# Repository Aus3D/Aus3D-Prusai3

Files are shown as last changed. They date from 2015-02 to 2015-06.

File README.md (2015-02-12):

# Aus3D's Prusa i3 Repository
This is the page for all of the documentation and firmware relating to the Aus3D [Prusa i3 3D Printer kit](http://aus3d.com.au/3D-printers/printer-kits/i3-printer).

The firmware is a version of Marlin pre-customised and calibrated to suit our i3 kit. It can be found in the 'Marlin-Marlin_v1' folder.

Documentation can be found in the folder labelled 'Docs'.

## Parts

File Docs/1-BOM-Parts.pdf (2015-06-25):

# Aus3D Prusa Mendel i3 Kit

## (HC-101 Acrylic Frame 3D Printer)

## Bill of Materials

(Updated 4/12/2014)

### Congratulations on receiving your Aus3D Prusa Mendel i3 kit!

Each kit is checked before being sent out, but before you start building you should confirm you have

### all of the below components. If something is missing, let us know and we’ll fix it!

Electronics | | Extruder
Power Supply | 1 | Stepper Motor | 1
Melzi Controller | 1 | Hotend | 1
Stepper Motor (w/ leadscrew) | 2 | Thermistor | 1
Stepper Motor (w/GT2 pulley) | 2 | Ceramic Heater | 1
Heated Bed (w/ Thermistor and wires) | 1 | 40mm Fan | 1
Endstop | 3
AU Power Cable | 1 | Hardware
USB Cable | 1 | Acrylic Frame Pieces*
Silicone Wire | 1 | Bed Support Plate | 1
| | 8mm Smooth Rod | 6
Printed Parts | | M8 Threaded Rod | 4
X Motor Mount | 1 | M3 Screws (several sizes) | Packs
X Idler | 1 | M3 Nuts | Pack
Y Bearing Holder (attached to Bed Support Plate) | | M3 Spring Washers | Pack
Endstop Clip | 3 | M8 Nuts | 6
| | M8 Washers | 4
| | GT2 Belt | 2m
Misc. | | Spring | 4
Spiral Wire Wrap | 1 | Bearing (flanged) | 2
Cable Ties | Pack
Cable Tie Mounts | Pack
Kapton Tape | Roll | Tools
USB | 1 | Allen Key | 4
PLA Filament Sample | 1 | Side Cutters | 1

*See included acrylic pieces bill-of-materials

*** Aus3D does not replace missing parts reported more than 30 days after date of delivery ***

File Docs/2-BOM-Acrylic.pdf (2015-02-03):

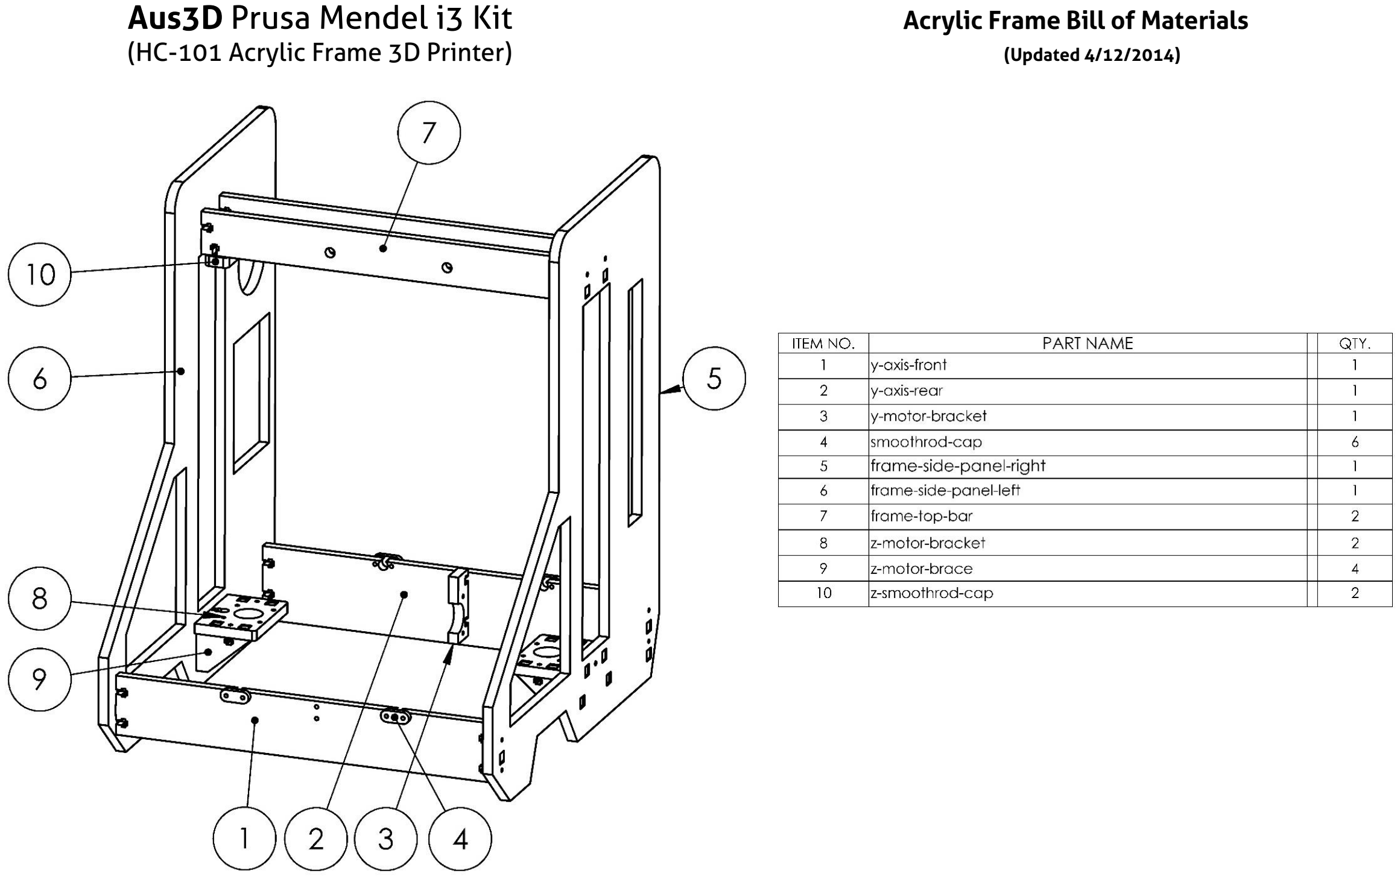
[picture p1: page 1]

Aus3D Prusa Mendel i3 Kit | Acrylic Frame Bill of Materials
(HC
-101 Acrylic Frame 3D Printer
) | (Updated 4/12/2014)

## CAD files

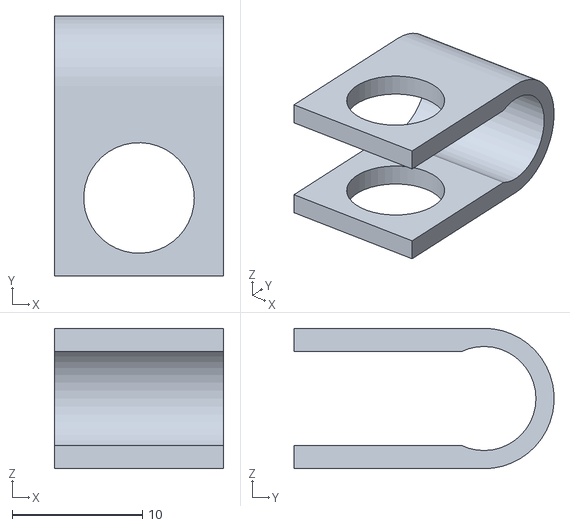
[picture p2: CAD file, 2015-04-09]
FrameSTLs/filament-clip.STL
13.0 x 20.0 x 10.8

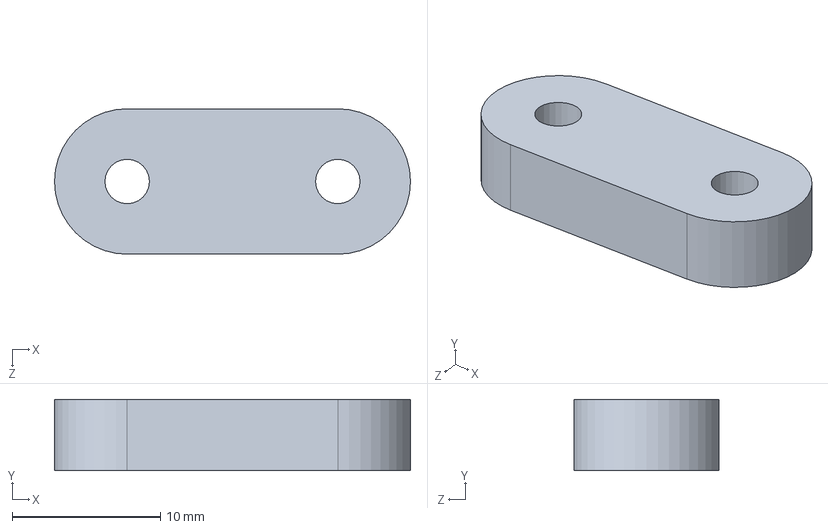
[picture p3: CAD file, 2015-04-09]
FrameSTLs/Source/smoothrod-cap.SLDPRT
24.0 x 4.80 x 9.80 mm

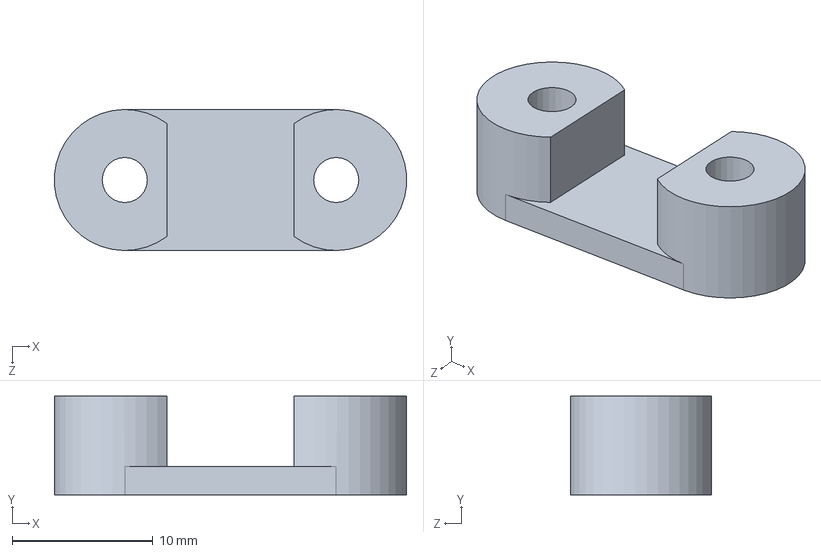
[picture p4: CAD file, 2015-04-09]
FrameSTLs/Source/y-belt-holder.SLDPRT
25.0 x 7.00 x 10.0 mm

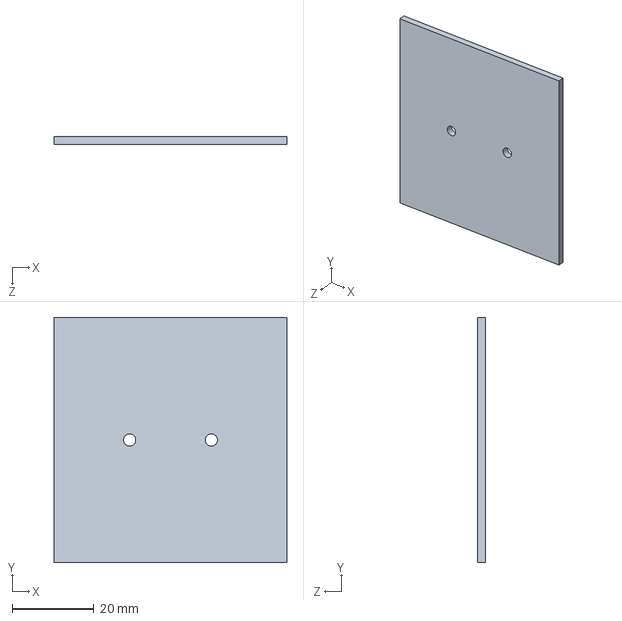
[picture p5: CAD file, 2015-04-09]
FrameSTLs/Source/extruderPlate.SLDPRT
57.0 x 60.0 x 2.00 mm

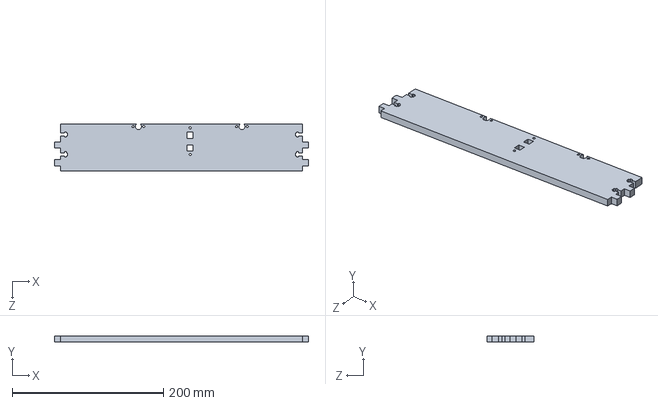
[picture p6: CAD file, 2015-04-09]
FrameSTLs/Source/y-axis-rear.SLDPRT
336.0 x 8.40 x 62.0 mm

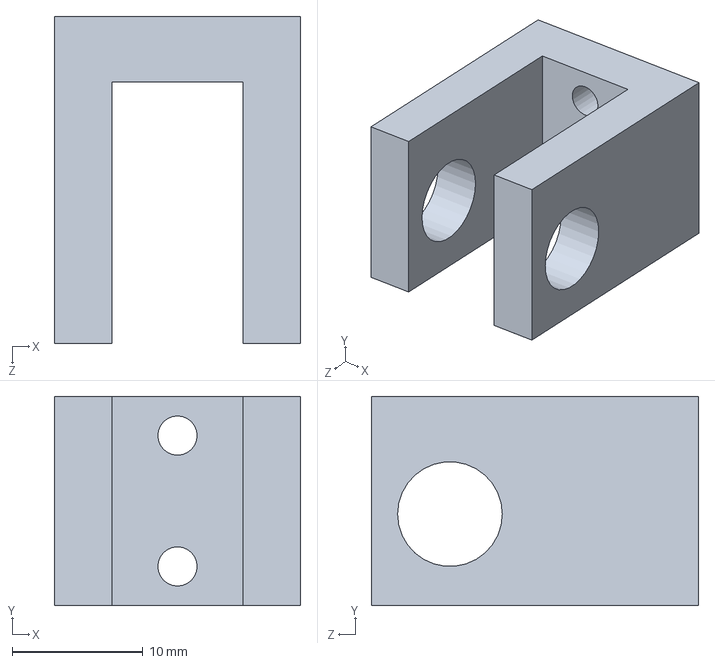
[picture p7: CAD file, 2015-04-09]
FrameSTLs/Source/y-idler.SLDPRT
18.8 x 16.0 x 25.0 mm

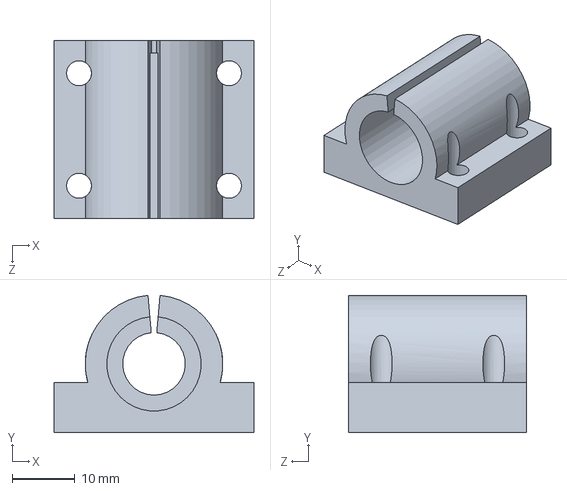
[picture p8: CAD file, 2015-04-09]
FrameSTLs/Source/y-bed-bearing-holder.SLDPRT
32.0 x 22.0 x 28.5 mm

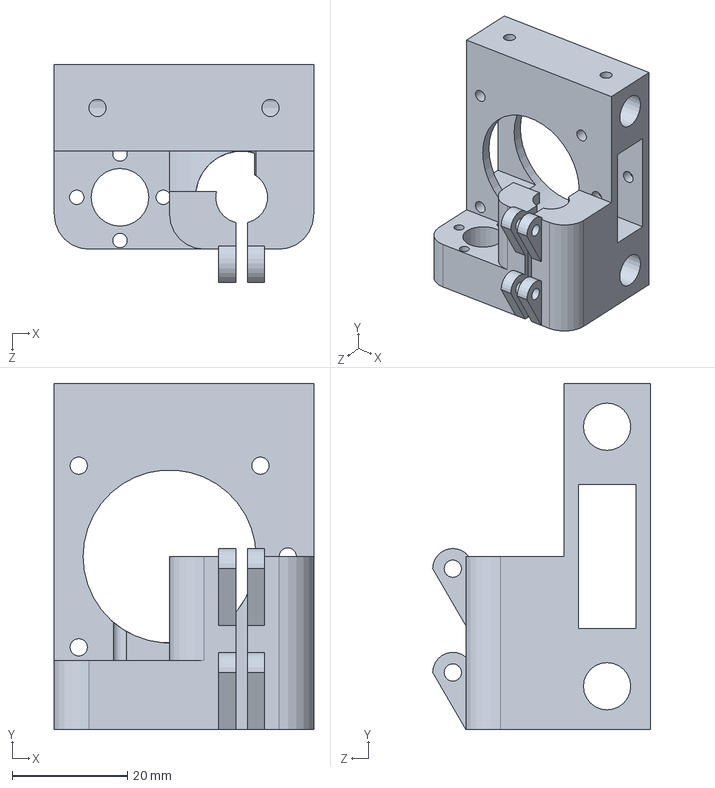
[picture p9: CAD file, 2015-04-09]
FrameSTLs/Source/x-motor-mount-new.SLDPRT
45.0 x 60.0 x 37.8 mm

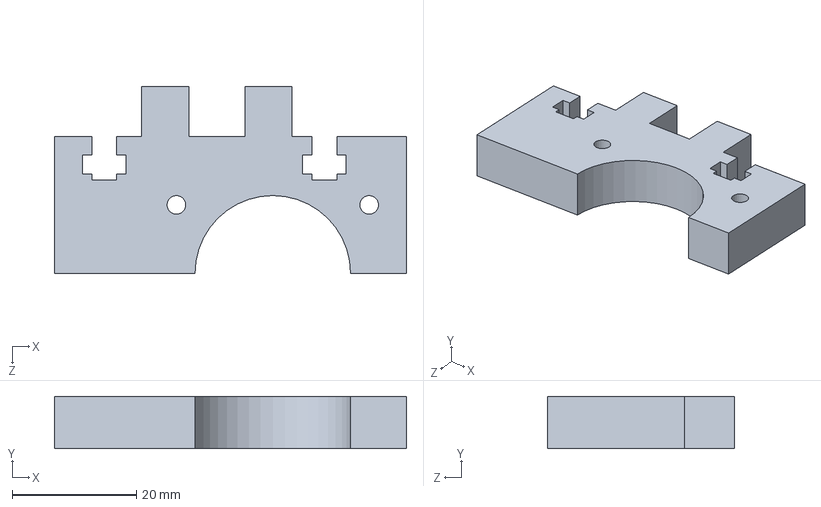
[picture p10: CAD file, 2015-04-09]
FrameSTLs/Source/y-motor-bracket.SLDPRT
56.6 x 8.40 x 30.0 mm

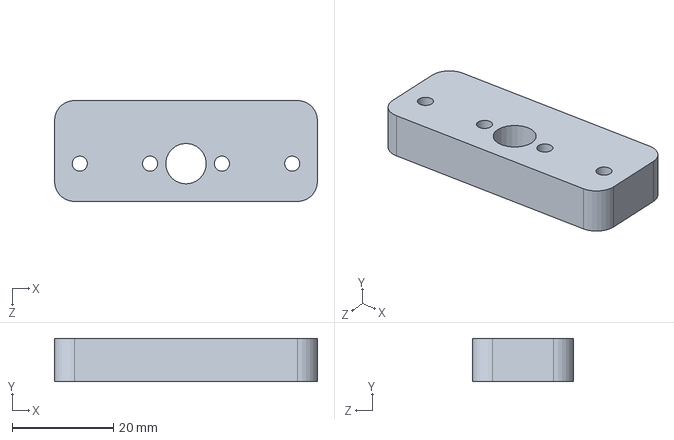
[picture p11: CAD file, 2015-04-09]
FrameSTLs/Source/z-smoothrod-cap.SLDPRT
52.0 x 8.60 x 20.0 mm

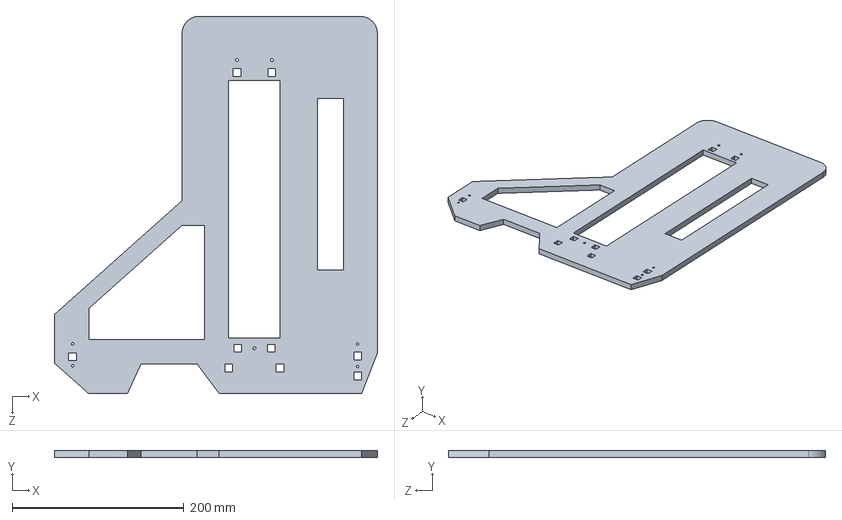
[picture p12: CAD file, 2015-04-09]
FrameSTLs/Source/frame-side-panel.SLDPRT
376.5 x 8.40 x 439.9 mm

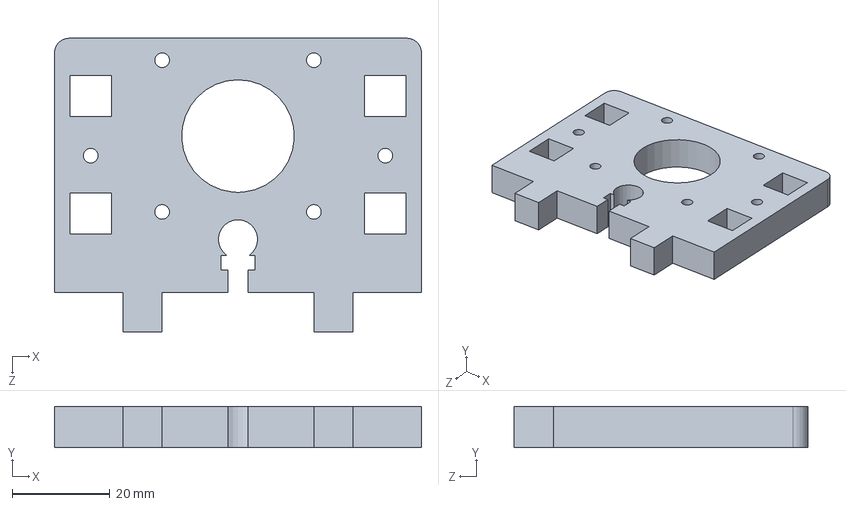
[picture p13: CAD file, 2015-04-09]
FrameSTLs/Source/z-motor-bracket.SLDPRT
75.0 x 8.40 x 60.0 mm

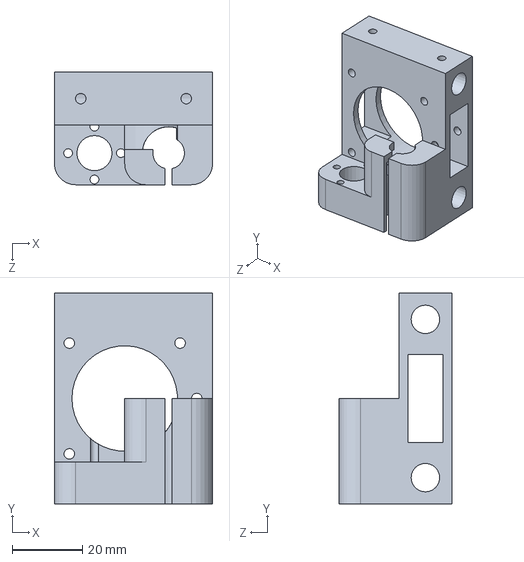
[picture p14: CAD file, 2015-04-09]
FrameSTLs/Source/x-motor-mount.SLDPRT
45.0 x 60.0 x 32.0 mm

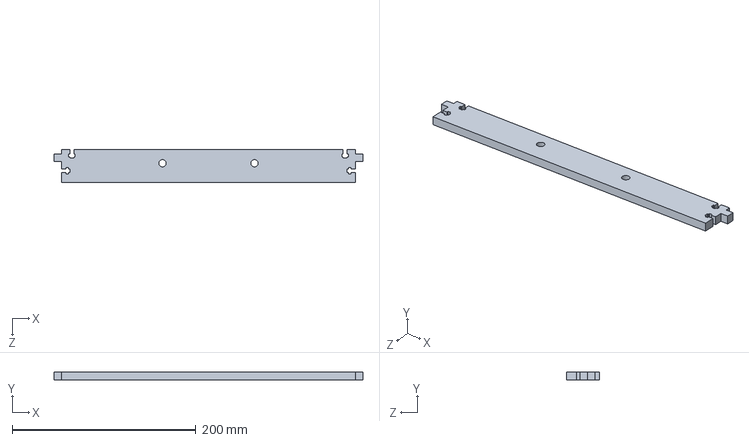
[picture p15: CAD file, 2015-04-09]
FrameSTLs/Source/frame-top-bar.SLDPRT
336.0 x 8.40 x 36.0 mm

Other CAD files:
FrameSTLs/Source/x-idler-mount.SLDPRT
FrameSTLs/Source/frame-side-panel-right.SLDPRT
FrameSTLs/Source/z-motor-brace.SLDPRT
FrameSTLs/Source/y-axis-front.SLDPRT
FrameSTLs/Source/frame-side-panel-left.SLDPRT
FrameSTLs/Source/x-idler-mount-new.SLDPRT
FrameSTLs/Source/y-support-plate.SLDPRT
FrameSTLs/frame-side-panel-left.STL
FrameSTLs/frame-side-panel-right.STL
FrameSTLs/frame-top-bar.STL
FrameSTLs/smoothrod-cap.STL
FrameSTLs/x-idler-mount.STL
FrameSTLs/x-motor-mount.STL
FrameSTLs/y-axis-front.STL
FrameSTLs/y-axis-rear.STL
FrameSTLs/y-bed-bearing-holder.STL
FrameSTLs/y-belt-holder.STL
FrameSTLs/y-idler.STL
FrameSTLs/y-motor-bracket.STL
FrameSTLs/y-support-plate.STL
FrameSTLs/z-motor-brace.STL
FrameSTLs/z-motor-bracket.STL
FrameSTLs/z-smoothrod-cap.STL

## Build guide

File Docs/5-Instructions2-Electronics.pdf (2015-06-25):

© 2015 Aus3D, All Rights Reserved. | V1.1

## Aus3D Prusa Mendel i3 Kit

Electronics Assembly Instructions

Section 1 - Electrical

1. Complete frame construction – see “instructionsV1.pdf”.
2. Install the power supply unit (PSU). The PSU mounts to the left side of the frame, and

# uses 4 M3 screws. Make sure to use the plastic spacers included - the screws shouldn't go too far (more than 3-4mm) inside the PSU. The electrical connections should face

downwards to make for neater cabling.
3. Install the Melzi control board. The control board mounts to the right side of the frame.

Plastic spacers are included in each kit, place spacers between the board and the frame before screwing it in place. Mount the control board so that the USB and microSD connections are near the top.
4. Install the cable that carries power from the PSU to the control board. This is a 2-core

cable (usually red and black). On the control board, the cable wires into the terminal marked “POWER”. The upper connection (near “HOTBED”) is negative, the lower connection (near “E-MOTOR”) is positive.

On the PSU the red wire should go to any of the DC Output terminals marked positive, and the black to any marked negative. All the positive terminals are identical, and all the negative terminals are identical – there is no preference where the wires connect, but keeping them further apart may reduce the risk of an accidental short.
5. Wire the motors to the control board. There are two different sets of coloured wires that

the motors may have. Depending which colours are present, wire the motor cables in the following order (top-to-bottom):

Black, Green, Blue, Red
or
Yellow, Blue, Green, Red

Motors wired incorrectly may move in reverse, or not move at all. However, there is no risk of damaging the motors due to incorrect wiring order.

If a motor runs in reverse, switch the first (or last, but not both) two wires around (e.g. swap black and green, or yellow and blue).

Because there are two motors for the Z axis, they will both need to be wired into the same terminals. Twisting the ends of the wires (e.g. both sets of red, etc.) together may make this easier.

6. Install the heated bed. Use 4 longer M3 screws (20-24mm), a washer on top of the bed, a spring (not washer, full spring) in between the bed and the bed support plate, and a washer and nut beneath the bed support plate.

These screws can be adjusted to raise or lower each corner of the bed in order to get it level. The springs provide some protection should the hot-end crash into the print bed.

The power cable going to the heated bed (thicker wires) connects to the “HOTBED” terminal on the control board. Polarity matters, follow the convention established for the “POWER” terminal – the wire nearest “POWER” should be positive.

The two white wires from the heated bed are wired to the thermistor, and connect to the “BTEMP” terminal. Polarity does not matter.

To level the heated bed, move the extruder down until the nozzle is a paper’s width from the bed surface. Now, move the extruder from left to right and verify that the distance remains constant. Adjust if necessary. Move the printer bed back and forth, again, monitor the distance and adjust if necessary.

7. Wire the extruder (motor should already be done. If not, do it first). The white wires (thermistor) connect to “ETEMP”, polarity does not matter. The red wires (heating element) connect to “HOTEND”. Again, polarity does not matter. The fan wires connect to “FAN”, and polarity matters. The positive wire is near “HOTEND”.
8. Now it is time to install and wire up the endstops (microswitches). Included are three plastic clips that the endstops will screw onto. The clips will hold the endstops onto 8mm smooth rod, and should be tightened in place securely. Below is a diagram of endstop placement:

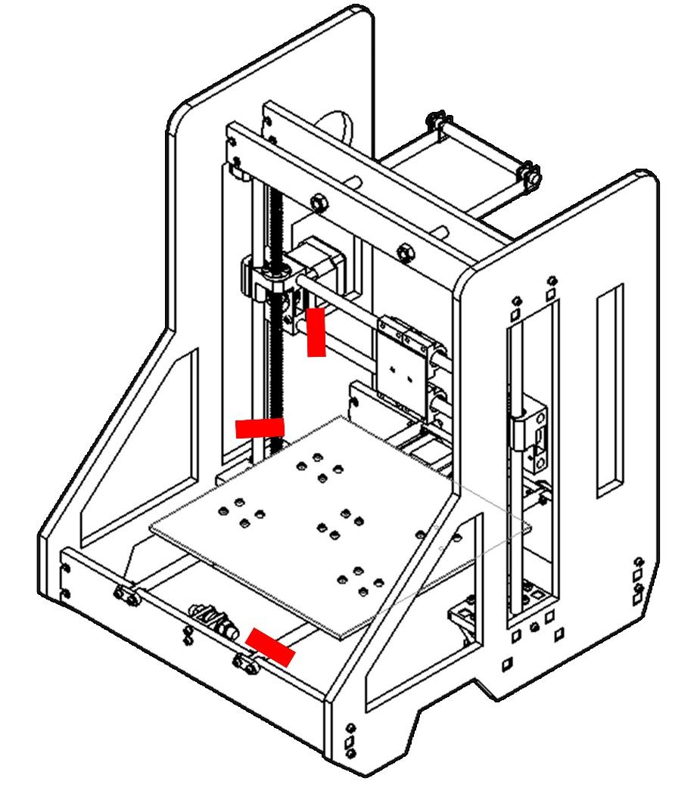
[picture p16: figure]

Verify that each switch will make contact with the moving components. The X endstop should be pressed by the extruder carriage, the Y endstop should be pressed by the printer bed, and the Z endstop should be pressed by the X motor mount.

Wire the endstops to the control board. Polarity does not matter. Endstops are marked “XSTOP”, “YSTOP” and “ZSTOP”.

9. Wire the included mains-lead to the PSU. For safety, ensure the cable is NOT connected to mains power while doing this step.

AU mains colour coding is as follows:

NEUTRAL – Black or Blue
LINE/ACTIVE – Red or Brown
EARTH – Green or Yellow

The PSU should have three terminals for the mains connection (AC Input), marked L, N and GND (or GND symbol, ).

Once the wires are securely in place, the cable may be plugged into mains power.

Section 2 – Software / Firmware

# 1. Download the Arduino IDE (version 1.0.5 recommended) from:

http://arduino.cc/en/Main/Software

2. Download the “Sanguino” folder from https://github.com/reprappro/Marlin. To do this, use the “Download Zip” button on the right of the page, and extract the “sanguino” folder somewhere you can find it.

Place the “sanguino” folder into Arduino hardware folder. On Windows, this is found at: C:\Users\USERNAME\Documents\Arduino\hardware

This should make the new structure C:\Users\USERNAME\Documents\Arduino\hardware\sanguino

3. Turn the power to the printer (mains power) on, and connect the USB cable between the printer and your computer. Your computer should automatically download and install the appropriate drivers. If not, drivers can be found on this USB.
4. Download the Aus3D customised firmware from https://github.com/Aus3D/Prusai3. Use the “Download ZIP” button as before. Extract the files, and open “Marlin.ino” with the Arduino software.
5. In the Arduino software, select the open file “Configuration.h” from the top bar of open files. The following lines will need to be adjusted later to properly calibrate distances:

// default settings
#define DEFAULT_AXIS_STEPS_PER_UNIT {78.7402,78.7402,200.0*8/3,760*1.1}

#define DEFAULT_MAX_FEEDRATE | {500, 500, 5, 25} // (mm/sec)

#define DEFAULT_MAX_ACCELERATION | {9000,9000,100,10000}

6. In the Arduino software, select “Tools”>”Board”>”Melzi 1284p 16mhz”.
Select “Tools”>”Serial Port”, and select the highest-numbered COM port.
7. Press the “Upload” (play) button to upload the firmware to the board. It may take a minute, but there should be a message informing you of a successful upload in the bottom terminal window. If there is not:
a. Double check the COM port. Verify this is the correct COM port by opening device manager and looking for Melzi. Alternatively, unplug the board to see which COM port disappears.
b. If problems persist, unplug the USB cable, wait a few seconds, and plug it back in. Select the correct COM port and try again.
c. Sometimes pressing the “Reset” button on the Melzi board before / during the start of the upload can help resolve issues.
8. Download the latest version of Printrun (or use the copy provided on the USB) and extract the software. Open “Pronterface”.

9. In Pronterface, set the Port to the known COM port, and the number (BAUD rate) to 115200 (which was pre-set in the firmware we uploaded). Press connect, and after a moment the console window in Pronterface should report success.
10. Position the extruder (by hand) in the middle of the X axis, so that if it moves the wrong way nothing will be damaged. Then, in Pronterface, use either the + or – X button to move the axis. Move the axis in short motions at first, until you are sure it is moving correctly. Do not move the axis far enough to crash into the frame.
11. Perform the same check for the Y and Z axis. They should each move as told. If any of the axis seem to move in the wrong direction, you can either switch the motor wires (as discussed previously) or change the firmware line (select appropriate axis, change false->true or vice-versa):

#define INVERT_X_DIR false

12. Now, test that the X axis homes correctly. Be ready to unplug mains power quickly, if something goes wrong here the printer will make an unpleasant sound – but it shouldn’t be damaged.

Move the extruder to the middle of the axis (electronically), and then press the X home button (X with a house). The carriage should move towards the switch, and once it presses the switch, it should stop moving.

If the axis moves the wrong way (away from the switch), verify:
-Where the switch was placed, relative to the diagram previously.
-That the motor moves in the correct direction under manual control.

If the axis does not stop, verify:
-That the carriage physically presses the switch on contact.
-That the switch is wired to the control board correctly.
13. Repeat these checks for the Y and Z axes. Again, be prepared to unplug the printer if something goes wrong.
14. Once each endstop has been tested and confirmed working, you may home all three axes. Press the home button without a letter – first the X axis will home, then Y, and then Z. This will happen automatically at the start of every print, so verify that no cables are going to get caught or stuck during this motion.
15. When an axis is homed, software defined limits are placed at the opposite end of the axis. The firmware included comes with limits of 150mm for the X any Y axis, and 180mm for the Z axis. Be ready with the power switch just in case! Verify that these limits are working by telling the software to move an axis repeatedly away from the endstop. Before the axis reaches the end, it should stop automatically, and not move any further.

These limits are pre-set as safe limits for getting setup and testing. To change these limits, edit the following lines in the firmware:

// Travel limits after homing #define X_MAX_POS 150
#define X_MIN_POS 0

#define Y_MAX_POS 150

#define Y_MIN_POS 0

#define Z_MAX_POS 180

#define Z_MIN_POS 0

16. Verify that the thermistors are operating correctly. The “Check Temp” button should return the temperature for the extruder and the bed.
17. Verify that the extruder and bed can both heat up correctly. Set the temperature to a full integer (60 for bed, 180 for extruder are common numbers for PLA) and press “Set”. You should see the temperature reach these numbers over a few minutes.

Do not touch the hotend while it is heating up! The heated bed gets toasty too!

18. Once at temperature, carefully feed some PLA filament through the extruder and into the hotend. Once the filament is correctly placed, and there is a gap between the nozzle and the bed (raise the Z axis), press “Extrude”. The extruder motor should activate and push the filament into the hot-end.

You may need to press the button several times (or adjust the extrude length) before any filament comes out the nozzle. If the motor spins the wrong way, see previous info regarding reversing the motors.

Note: Pronterface will for some reason return an error message if the extruded length or rate are decimal values – ensure they are integer numbers with no decimal point.

19. Congratulations – at this stage, everything should be working and you should be ready to do a test print – and start calibrating! Calibration is far too broad a topic to be encompassed in this guide – an excellent starting point is the following wiki page:

http://reprap.org/wiki/Calibration

Finally, if you are stuck and need assistance, please contact me via chris@aus3d.com.au.

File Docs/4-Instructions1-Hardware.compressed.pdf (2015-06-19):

Components:
2M3x16Screws
2M3SpringWashers
2M3HexNuts
AssembledZbrackets
AcrylicSidePanels

Attachtheassembledmotorbrackets totheacrylicsidepiecesoftheframe.

Seethebelow imagesfororientation.

Components:
2M3x16Screws
2M3SpringWashers
2M3HexNuts
1Z-motor-bracket
2Z-motor-braces

RepeatforthesecondZmotorbracket. Theacryliccomponentshaveno orientationandareinterchangeable.

Components:
2M3x16Screws
2M3SpringWashers
2M3HexNuts
1Z-motor-bracket
2Z-motor-braces

AssemblethefirstZmotorbracket usingtheabovecomponents.Takecare nottoovertightenthescrews.

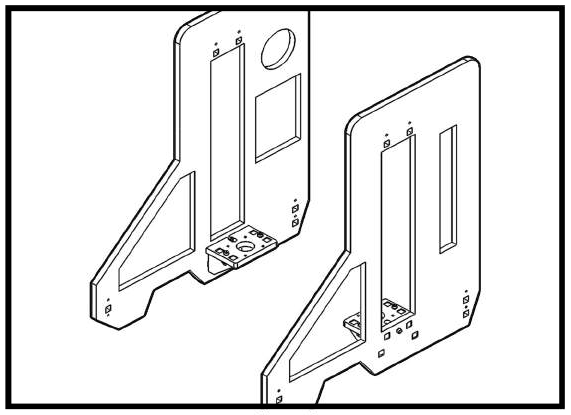
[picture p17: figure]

© 2015Aus3D,AllRightsReserved. | Page1

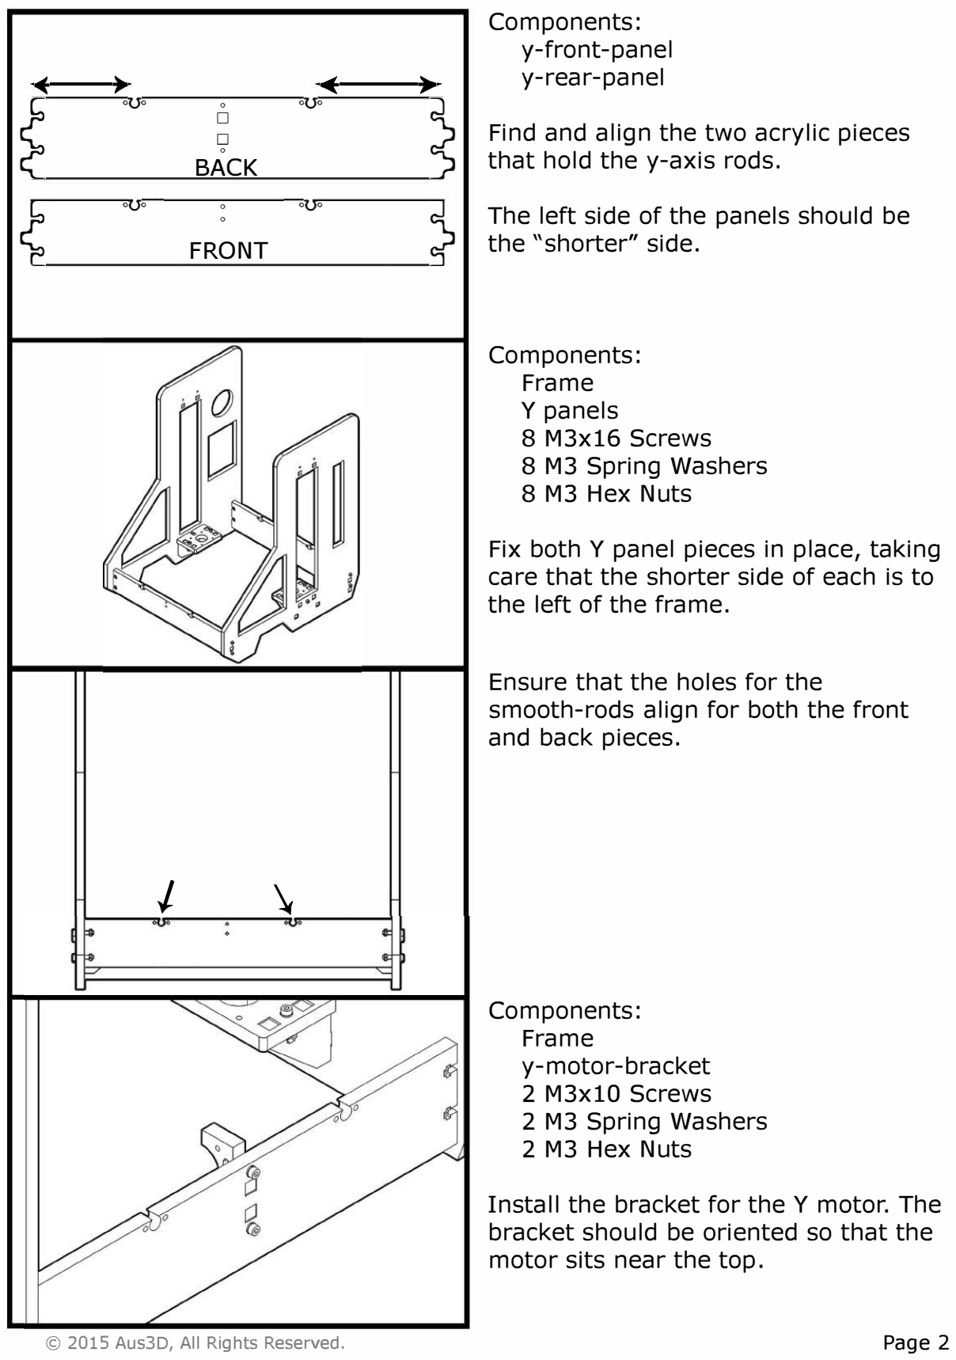
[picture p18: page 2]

-E |

ouo

ouo

0
D
D

0
BACK

0

0
FRONT

J \

ouo

ouo

© 2015 Aus3D, All Rights Reserved.

y-front-panel
y-rear-panel

Find and align the two acrylic pieces that hold the y-axis rods.

The left side of the panels should be the "shorter" side.

Components:
Frame
Y panels
8 M3x16 Screws
8 M 3 Spring Washers
8 M3 Hex Nuts

Fix both Y panel pieces in place, taking care that the shorter side of each is to the left of the frame.

Ensure that the holes for the smooth-rods align for both the front and back pieces.

Components:
Frame
y-motor-bracket
2 M3x10 Screws
2 M 3 Spring Washers
2 M3 Hex Nuts

Install the bracket for the Y motor. The bracket should be oriented so that the motor sits near the top.

Components:
BedSupportPlate
YBearingHolders(attachedtoabove)
28mm SmoothRods(~ 345mm)

Slidethesmoothrodsthroughthe frontY-plate,thenthroughtheY bearingholders(andbearings)and finallythroughtherearY-plate.

Checkthatthebedcanmovealongthe rods.

Components:
Frame
StepperMotor(longshaft)
2M3x12Screws
2M3SpringWashers

Checkthetwosteppermotorswith attachedpulleys.Insomekits,one motorhasalongershaft.Ifthisisthe case,usethismotor.

FixthismotortotheYmotormount.

Components:
Frame
y-idler
2M3x16Screws
2M3SpringWashers
2M3HexNuts

Attachthey-idlertothefronty-plate oftheframe.Thescrewsandnuts shouldnotinterferewiththebearings.

y-idler(plasticpart)
M8Rod(small)
2FlangedBearings
2M8Washers
2M8HexNuts

Fittheflangedbearingsintothey-idler asshown.

Theplasticpartmayneedtobe
cleaned/drilledout.

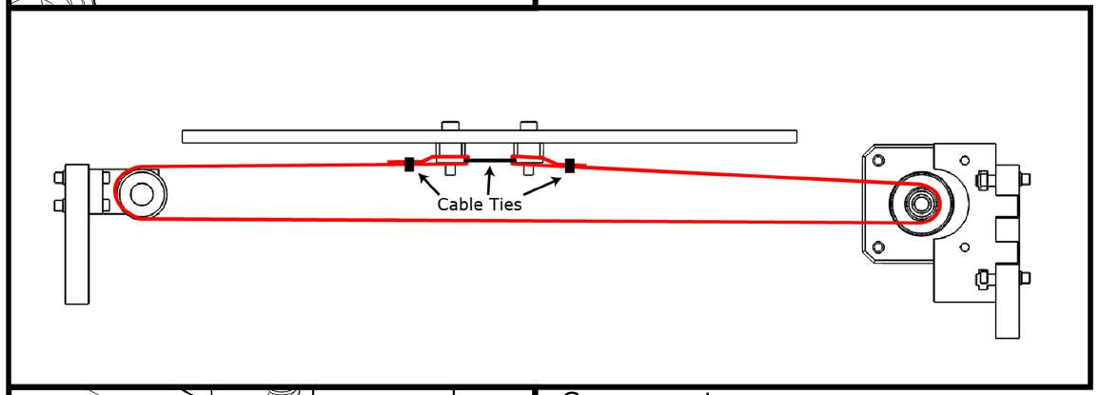
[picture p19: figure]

Components:
Frame
2Zmotors(withleadscrew)
8M3x14Screws
8M3SpringWashers

FixeachZmotortooneoftheZmotor brackets.

Removethecarriage-nutfrom each leadscrew.

Components:
Frame
GT2Belt(~ 0.8m)

Arrangethebeltasshowninthe diagram below.

Useacabletiebetweenthetwoends ofthebelttopullittaut.

Verifythatthebedcanmovefreely.

Frame
4Smoothrod-caps
8M3x16Screws
8M3SpringWashers
8M3HexNuts

Installthesmallacryliccappiecesat eachendofbothsmooth-rods.

Components:
XCarriage
XMotor(shortshaft)
3M3x14Screws
3M3SpringWashers

AttachtheXmotortothemountas shown.

Components:
XCarriage

SlidetheXCarriage(attachedtothe extruder)ontotheXaxissmoothrods.

PressthesmoothrodsintotheXIdler. Ifneccessary,carefullyhammerthe Idlerintoplace.

Components:
XMotorMount
XIdlerMount
28mm SmoothRods(~300mm)

PressbothsmoothrodsintotheX MotorMount.Theplasticmayneedto bedrilledslightlytoallow therodtofit.

Thefitshouldbefirm enoughto preventtherodsfrom movingfreely.

2CarriageNuts
XMotorMount
XIdler
8M3Screws

Installacarraigenutonboththe plasticpartsasshown.

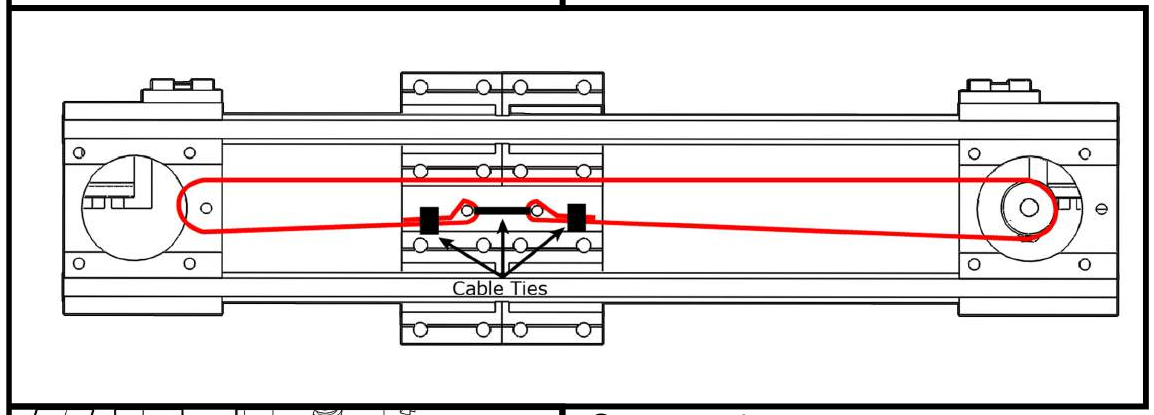
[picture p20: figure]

SlidetheX-axisontotheZ-axissmooth rods.Turntheleadscrew rodsbyhand tolowertheX-axis.

ManuallymovetheX-axisdown.Check thatitcanreachdowntothebed withoutissue.

Checkthedistancebetweenthe X-motormountandX-idlerifproblems occur.

Components:
Frame
28mm SmoothRods(~320mm)

InserttheZ-axissmoothrodsintothe cutoutsintheZmotorbrackets.The smoothrodsshouldsitonthe
Z-motors.Thescrew holdingthe Z-motorbracketsinplacemayneedto beloosenedslightly.

GT2Belt(~0.8m)
CableTies

InstalltheGT2beltontheXaxisas showninthebelow diagram.
(Diagram isreverseview,motoron right)

Usethecentercabletietotensionthe belt.

Pushtheplasticclipsontotheendof eachthreadedrod.

Slidethethirdthreadedrodthrough thefirstplasticclip.

Ifyouhaveaspooloffilamentready, placeitbetweentheclipsnow.

Pushtherodthroughthespooland intotheotherplasticclip.

Components:
Frame
3M8ThreadedRods
4M8Nuts
2PlasicSpoolClips

Slidethetwolongerthreadedrods throughthecutoutsinthetoppiecesof theframe,thenfixthem inplacewith theM8nuts.

Components:
Frame
2Z-smoothrod-caps
2Smoothrod-caps
4M3x16Screws
4M3SpringWashers
4M3HexNuts

FitthecapsthatholdtheZ-smoothrodsinplace.

Frame
2Frame-top-bars
4M3x16Screws
4M3SpringWashers
4M3HexNuts

Installthetwoacrylictop-barpieces ontotheframe.

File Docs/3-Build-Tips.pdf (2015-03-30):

Last updated: 30/3/2015 | V1.2

## Aus3D Prusa Mendel i3 Kit

(HC-101 Acrylic Frame 3D Printer)

Note: Copies of this documentation, along with other relevant files, can be found at: http://github.com/Aus3D/Prusai3 Tips:
- Use an included spring-washer on every bolt (where possible). This reduces the likelihood of damaging the acrylic.
- Take care not to over tighten any of the screws or bolts, as acrylic is not flexible and will snap suddenly if it experiences too much force. Generally, all screws and bolts should tighten until they feel fairly secure, do not tighten them further.
- Take care in aligning the acrylic supports for the y-axis – while they will fit in both ways, both the front and back must line up.
- Remember to put the y-axis printer bed support (large sheet with printed bearing holders) onto the 8mm smooth rods before fixing the smooth rods in place.
- Assemble the x-axis before placing it onto the z-rods.
- When wiring, take care to position all cables so that they will not get caught in moving parts. Cable ties, cable tie sticky mounts and cable loom is provided to help keep things tidy. Move each axis by hand to ensure cables will not get caught.
- Calibration is generally the hardest part of any printer build. Repetition is unfortunately the key, but a few things to check are:
- X/Y/Z axis are all as square as possible.
- Endstops are correctly positioned
- Hot-end nozzle is 1 layer height (0.2-0.4mm, use a sheet of paper to check) above printing surface.
- Bed is level (check each corner and centre)
- Some printed parts may vary slightly from kit to kit. Do not be alarmed if the parts you receive are not identical to those pictured in the assembly guide, as parts are revised and updated regularly.
- Screw sizes listed in the assembly manual are a guide only. The thickness of some parts varies from kit to kit, and different sized screws may need to be used. The included screws should be sufficient. Make sure screws used are long enough to thread into the nut, but not long enough to press into the acrylic frame (for T-slot joins).
- Finally, superglue works wonders on acrylic. Obviously it is better that none of the frame is damaged, but if something is over tightened, it can be fixed.

Warning: 3D Printers are complicated machines, and can be dangerous is mishandled. Parts of the printer reach high temperatures during use, and become dangerous to touch. Keep flammable items away from the printer during operation, and do not leave the printer unattended during operation. Running the printer in an enclosed environment (heating chamber, etc.) where heat is allowed to build up may damage the machine, and is not recommended.

If you are stuck and need assistance, please contact Chris via chris@aus3d.com.au.

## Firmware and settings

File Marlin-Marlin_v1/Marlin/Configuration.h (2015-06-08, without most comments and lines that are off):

#define CONFIGURATION_H
#define STRING_VERSION_CONFIG_H __DATE__ " " __TIME__ // build date and time
#define STRING_CONFIG_H_AUTHOR "(none, default config)" // Who made the changes.
#define SERIAL_PORT 0
#define BAUDRATE 115200
#define MOTHERBOARD 66
 #define CUSTOM_MENDEL_NAME "Aus3D Prusa i3"
#define EXTRUDERS 1
#define POWER_SUPPLY 1
#define TEMP_SENSOR_0 70
#define TEMP_SENSOR_1 0
#define TEMP_SENSOR_2 0
#define TEMP_SENSOR_BED 70
#define MAX_REDUNDANT_TEMP_SENSOR_DIFF 10
#define TEMP_RESIDENCY_TIME 10  // (seconds)
#define TEMP_HYSTERESIS 3       // (degC) range of +/- temperatures considered "close" to the target one
#define TEMP_WINDOW     1       // (degC) Window around target to start the residency timer x degC early.
#define HEATER_0_MINTEMP 5
#define HEATER_1_MINTEMP 5
#define HEATER_2_MINTEMP 5
#define BED_MINTEMP 5
#define HEATER_0_MAXTEMP 275
#define HEATER_1_MAXTEMP 275
#define HEATER_2_MAXTEMP 275
#define BED_MAXTEMP 150
#define PIDTEMP
#define BANG_MAX 255 // limits current to nozzle while in bang-bang mode; 255=full current
#define PID_MAX 255 // limits current to nozzle while PID is active (see PID_FUNCTIONAL_RANGE below); 255=full current
  #define PID_FUNCTIONAL_RANGE 10 // If the temperature difference between the target temperature and the actual temperature
  #define PID_INTEGRAL_DRIVE_MAX 255  //limit for the integral term
  #define K1 0.95 //smoothing factor within the PID
  #define PID_dT ((OVERSAMPLENR * 10.0)/(F_CPU / 64.0 / 256.0)) //sampling period of the temperature routine
    #define  DEFAULT_Kp 22.2
    #define  DEFAULT_Ki 1.08
    #define  DEFAULT_Kd 114
#define MAX_BED_POWER 255 // limits duty cycle to bed; 255=full current
#define PREVENT_DANGEROUS_EXTRUDE
#define PREVENT_LENGTHY_EXTRUDE
#define EXTRUDE_MINTEMP 170
#define EXTRUDE_MAXLENGTH (X_MAX_LENGTH+Y_MAX_LENGTH) //prevent extrusion of very large distances.
#define ENDSTOPPULLUPS // Comment this out (using // at the start of the line) to disable the endstop pullup resistors
  #define ENDSTOPPULLUP_XMAX
  #define ENDSTOPPULLUP_YMAX
  #define ENDSTOPPULLUP_ZMAX
  #define ENDSTOPPULLUP_XMIN
  #define ENDSTOPPULLUP_YMIN
  #define ENDSTOPPULLUP_ZMIN
const bool X_MIN_ENDSTOP_INVERTING = true; // set to true to invert the logic of the endstop.
const bool Y_MIN_ENDSTOP_INVERTING = true; // set to true to invert the logic of the endstop.
const bool Z_MIN_ENDSTOP_INVERTING = true; // set to true to invert the logic of the endstop.
const bool X_MAX_ENDSTOP_INVERTING = true; // set to true to invert the logic of the endstop.
const bool Y_MAX_ENDSTOP_INVERTING = true; // set to true to invert the logic of the endstop.
const bool Z_MAX_ENDSTOP_INVERTING = true; // set to true to invert the logic of the endstop.
#if defined(COREXY) && !defined(DISABLE_MAX_ENDSTOPS)
  #define DISABLE_MAX_ENDSTOPS
#endif
#define X_ENABLE_ON 0
#define Y_ENABLE_ON 0
#define Z_ENABLE_ON 0
#define E_ENABLE_ON 0 // For all extruders
#define DISABLE_X false
#define DISABLE_Y false
#define DISABLE_Z false
#define DISABLE_E false // For all extruders
#define DISABLE_INACTIVE_EXTRUDER true //disable only inactive extruders and keep active extruder enabled
#define INVERT_X_DIR false    // for Mendel set to false, for Orca set to true
#define INVERT_Y_DIR true    // for Mendel set to true, for Orca set to false
#define INVERT_Z_DIR false     // for Mendel set to false, for Orca set to true
#define INVERT_E0_DIR true   // for direct drive extruder v9 set to true, for geared extruder set to false
#define INVERT_E1_DIR false    // for direct drive extruder v9 set to true, for geared extruder set to false
#define INVERT_E2_DIR false   // for direct drive extruder v9 set to true, for geared extruder set to false
#define X_HOME_DIR -1
#define Y_HOME_DIR -1
#define Z_HOME_DIR -1
#define min_software_endstops true // If true, axis won't move to coordinates less than HOME_POS.
#define max_software_endstops true  // If true, axis won't move to coordinates greater than the defined lengths below.
#define X_MAX_POS 150
#define X_MIN_POS 0
#define Y_MAX_POS 150
#define Y_MIN_POS 0
#define Z_MAX_POS 180
#define Z_MIN_POS 0
#define X_MAX_LENGTH (X_MAX_POS - X_MIN_POS)
#define Y_MAX_LENGTH (Y_MAX_POS - Y_MIN_POS)
#define Z_MAX_LENGTH (Z_MAX_POS - Z_MIN_POS)
#define Z_PROBE_REPEATABILITY_TEST  // If not commented out, Z-Probe Repeatability test will be included if Auto Bed Leveling is Enabled.
#define MANUAL_X_HOME_POS 0
#define MANUAL_Y_HOME_POS 0
#define MANUAL_Z_HOME_POS 0
#define NUM_AXIS 4 // The axis order in all axis related arrays is X, Y, Z, E
#define HOMING_FEEDRATE {50*60, 50*60, 150, 0}  // set the homing speeds (mm/min)
#define DEFAULT_AXIS_STEPS_PER_UNIT   {78.7402,78.7402,400,105}  //steps per unit
#define DEFAULT_MAX_FEEDRATE          {500, 500, 3, 25}    // (mm/sec)
#define DEFAULT_MAX_ACCELERATION      {9000,9000,100,10000}    // X, Y, Z, E maximum start speed for accelerated moves. E default values are good for Skeinforge 40+, for older versions raise them a lot.
#define DEFAULT_ACCELERATION          3000    // X, Y, Z and E max acceleration in mm/s^2 for printing moves
#define DEFAULT_RETRACT_ACCELERATION  3000   // X, Y, Z and E max acceleration in mm/s^2 for retracts
#define DEFAULT_XYJERK                20.0    // (mm/sec)
#define DEFAULT_ZJERK                 0.4     // (mm/sec)
#define DEFAULT_EJERK                 5.0    // (mm/sec)
#define CUSTOM_M_CODES
  #define CUSTOM_M_CODE_SET_Z_PROBE_OFFSET 851
  #define Z_PROBE_OFFSET_RANGE_MIN -15
  #define Z_PROBE_OFFSET_RANGE_MAX -5
#define PLA_PREHEAT_HOTEND_TEMP 180
#define PLA_PREHEAT_HPB_TEMP 70
#define PLA_PREHEAT_FAN_SPEED 255   // Insert Value between 0 and 255
#define ABS_PREHEAT_HOTEND_TEMP 240
#define ABS_PREHEAT_HPB_TEMP 100
#define ABS_PREHEAT_FAN_SPEED 255   // Insert Value between 0 and 255
#define SOFT_PWM_SCALE 0
#define FILAMENT_SENSOR_EXTRUDER_NUM	0  //The number of the extruder that has the filament sensor (0,1,2)
#define MEASUREMENT_DELAY_CM			14  //measurement delay in cm.  This is the distance from filament sensor to middle of barrel
#define DEFAULT_NOMINAL_FILAMENT_DIA  3.0  //Enter the diameter (in mm) of the filament generally used (3.0 mm or 1.75 mm) - this is then used in the slicer software.  Used for sensor reading validation
#define MEASURED_UPPER_LIMIT          3.30  //upper limit factor used for sensor reading validation in mm
#define MEASURED_LOWER_LIMIT          1.90  //lower limit factor for sensor reading validation in mm
#define MAX_MEASUREMENT_DELAY			20  //delay buffer size in bytes (1 byte = 1cm)- limits maximum measurement delay allowable (must be larger than MEASUREMENT_DELAY_CM  and lower number saves RAM)
#define DEFAULT_MEASURED_FILAMENT_DIA  DEFAULT_NOMINAL_FILAMENT_DIA  //set measured to nominal initially
#include "Configuration_adv.h"
#include "thermistortables.h"

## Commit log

2014-12-16 Initial Commit
    Adding current revision of Marlin firmware customised for Aus3D Prusa i3
    printer.
    [Configuration.h, Configuration_adv.h, Menu Plans.xlsx]
2014-12-23 Updated for new thermistor
    [Configuration.h]
2014-12-23 Added thermistor table for i3 kit
    Kits are now shipping with different thermistor, measured and calculated thermistor table for firmware.
2015-01-30 Update Configuration.h
    Updated default steps per unit to suit current i3 kit.
    [Configuration.h]
2015-02-03 Added documentation
    Added documentation to repository. Also added relevant drivers and
    software.
2015-04-09 Added Frame Files
    Added STL files for frame components.
    [filament-clip.STL, frame-side-panel-left.STL, frame-side-panel-right.STL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]
2015-04-09 Added Frame Source
    Added SolidWorks source files for frame / printed components.
    [extruderPlate.SLDPRT, frame-side-panel-left.SLDPRT, frame-side-panel-right.SLDPRT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]
2015-04-27 Arduino IDE
    Recommend Arduino IDE 1.0.5 as newer versions require different steps
    for board hardware setup.
2015-04-27 Numbered Documents
    Numbered Docs for readability / assembly order
2015-05-06 Update Z feedrate
    Reported issues with Z feed rate and homing rate being too quick causing steppers to stall or vibrate in place. Has not been replicated, but figures adjusted to more reasonable levels.
    [Configuration.h]
2015-05-21 Added PSU spacer note
2015-05-21 Added OSX Driver (Beta / Experimental)
2015-06-08 Correct Extruder Value
    Old value was based off of older hardware. Updated for newer kits.
    [Configuration.h]
